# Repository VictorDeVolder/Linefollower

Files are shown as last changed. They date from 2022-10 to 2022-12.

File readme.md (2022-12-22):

# LineFollower
<br />
<br />
[picture]

<br />
<br />
  
## specifications
<br />
microcontroller: ATmega328 5V 16 MHz 
<br />
motors: Micro motor N20-BT21 9V-30:1-1000rpm
<br />
h-bridge: HALJIA DRV8833 1,5A 2 kanalen H-Bridge
<br />
sensors: QTR-8A reflectiesensorarray
<br />
batteries: 2x Quickstuff 18650 batterijen 
<br />
wireless communication: AZDelivery HC-05 Bluetooth module 
<br />
distance sensor - motors: 12,5cm 
<br />
weight: 210g
<br />
speed: 0,774 m/s 
<br />

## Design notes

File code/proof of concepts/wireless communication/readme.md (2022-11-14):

# draadloze communicatie proof of concept
minimale hard- en software waarmee aangetoond wordt dat duplex kan gecommuniceerd worden tussen de microcontroller en een smartphone, gebruik makend van HC-05 programma. 
<br />
### configuratie
Draadloze communicatie voor led aan/ uit zetten.

### opmerkingen
Correcte bautrate instellen.

### gebruiksaanwijzing
Zie datasheet.

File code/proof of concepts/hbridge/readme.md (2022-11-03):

# H-Bridge proof of concept

minimale hard- & software die aantoont dat 2 motoren onafhankelijk van elkaar kunnen draaien, en (traploos) regelbaar zijn in snelheid en draairichting.

aansturen van de DRV8833 H-brug

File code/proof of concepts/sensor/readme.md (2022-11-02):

# Sensoren proof of concept

minimale hard- en software die aantoont dat minimaal 6 sensoren onafhankelijk van elkaar kunnen uitgelezen worden en dat daarbij een zo groot mogelijk bereik van de AD converter benut wordt (indien van toepassing)

Uitlezing van 8 analoge sensoren: QRT-8a sensor

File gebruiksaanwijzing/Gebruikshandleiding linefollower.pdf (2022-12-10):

# Gebruikshandleiding linefollower

## Syntheseproject

Academiejaar 2022-2023

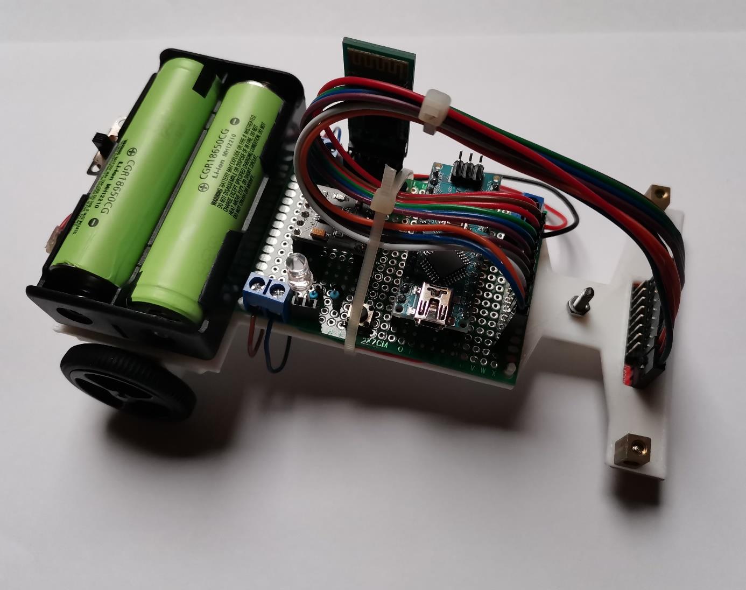
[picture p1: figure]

Naam: Victor De Volder

Klasgroep: 3AMB

Gebruikshandleiding linefollower:
Volg de volgende stappen om een correcte werking te bekomen.

Stap1:
Upload de finale code.

Stap2:
Schakel de hoofdschakelaar, deze bevindt zich achteraan de wagen.

Stap3: Connecteren
Download en open de app Serail Bluetooth Terminal. Klik op de navigation drawer en ga naar Devices. Connecteer vervolgens met de bluetooth module onder de naam HC-05 (98:D3:51:F5:EF:E6). Als alles goed verlopen is komt er in Terminal connected te staan.

Stap4: Commando’s

- Debug
Het commando debug geeft alle ingestelde parameters weer en de sensorwaarden.
- Set power, diff, kp, ki, kd, cycle.
De Set commando maakt het mogelijk om de ingestelde waardes van de weergegeven parameters te wijzigen.
- run
De linefollower begint te rijden.
- stop
De linefollower zal direct stoppen.
- Calibrate black
Zwart waarden kalibreren van de sensor.
- Calibrate white
Wit waarden kalibreren van de sensor.

Stap5: Kalibreren
Positioneer de sensoren boven een zwart vlak en voer het commando calibrate black uit in de Terminal. Breng vervolgens de sensoren boven een wit vlak en voer het commando calibrate white uit. De sensoren zijn nu gekalibreerd.

Stap6: Parameters instellen
Stel de gewenste parameters in met het commando Set … .

Ingestelde parameters:

- cycle time: 2000
- Power: 145
- diff: 0.20
- kp: 10
- ki: 0.20
- kd: 0.40

Stap7: Starten
Voer het commando run uit en de wagen zal de lijn beginnen volgen met een gemiddelde snelheid van 0.774 m/s.

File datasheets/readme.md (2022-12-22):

datasheets of the components used in this project

Datasheets zijn terug te vinden bij de proof of consepts.

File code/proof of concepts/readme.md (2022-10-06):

# Proof of Concepts

Een proof of concept is een combinatie van minimale hard- en software om eenvoudig aan te tonen dat iets werkt.  
Proof of concepts kunnen enerzijds als eerste poging dienen om een bepaald onderdeel van het project werkend te krijgen. Anderzijds kunnen ze tijdens het debuggen van het finale project dienen als test om eventuele hardware problemen te elimineren bij onduidelijke problemen.
<br />  
<br />
Een proof of concept bestaat uit
* een elektronisch schema (indien van toepassing)
* minimale code om de voorop gestelde zaken te demonstreren
* minimale uitleg / aandachtspunten
<br />
De elektronische schakelingen van de proof of concepts komen bij voorkeur overeen met deze van de uiteindelijke linefollower, zodat de code zonder aanpassingen op het finale project kan draaien.

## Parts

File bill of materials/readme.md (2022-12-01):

## bill of materials
<br />

|volgnummer|naam|omschrijving|nieuw/recup|kostprijs/stuk|aantal|subtotaal|
|---|----|---|---|---|---|---|
| 1| Micro motor N20-BT21 9V |  1000 rpm - 30:1  | nieuw | € 5,40 | 2  | € 10,80 |
| 2| 18650 batterijhouder dubbel |Lengte = 7,6cm; Breedte = 4,1cm; Hoogte = 2cm;| nieuw | € 1,39 | 1 | € 1,39 |
| 3| 2x Quickstuff 18650 batterijen plus oplader |2x 18650 3,7V 3000 mah oplaadbare batterijen | nieuw | € 22,95 | 1 | € 22,95 |
| 4| QTR-8A reflectiesensorarray - analoog - Pololu 960 | 8 sensoren; Analoog; Voedingsspanning: 5V of 3,3V | nieuw | € 11,91 | 1 | € 11,91 |
| 5| AZDelivery Nano V3.0 Mini USB Board | ATmega328 5V 16 MHz | nieuw | € 5,39 | 1 | € 5,39 |
| 6| HALJIA DRV8833 1,5A 2 kanalen H-Bridge | DC Gear motor driver module board; 2,7 tot 10,8V DC; Uitgangsstroom max 4A | nieuw | € 2,99 | 1 | € 2,99 |
| 7| Wielen 32x7mm Pololu | diameter 32mm, breedte 7mm | nieuw | € 4,32  | 2 | € 4,32 |
| 8| Akozon printplaat gatenroosterplaat | 5cm x 7cm dubbelzijdige prototyping-printplaat | nieuw | € 1,22 | 1 | € 1,22 |
| 9| Terminal blok connector | Pitch: 5,08mm; 5,08-301-2P, nominale spanning: 300V, nominale stroom: 16A | nieuw | € 0,27 | 3 | € 0,81 |
| 10| AZDelivery HC-05 Bluetooth Wireless RF Transceiver module | bereik max 10m, bluethooth klasse 2| nieuw | € 3,99 | 1 | € 3,99 |
| 11| Drukknopschakelaar | Bedrijfspanning = 250V; Connectortype = through hole; Merk Youmile  | recup | / | 1 | / |
| 12| Weerstand | 220 ohm | recup | / | 1 | / |
| 13| Weerstand | 1K ohm | recup | / | 4 | / |
| 14| Aan/ uit schakelaar batterij| / | recup | / | 1 | / |
| 15| Bout & moer | M5x22mm | recup | / | 1 | / |
| 16| Bout & moer | M2.5x14mm | recup | / | 6 | / |
| 17| Onderstel | PLA | recup | / | 1 | / |
| | | | | |Totaal | € 65,77 |

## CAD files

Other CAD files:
technische tekeningen/mechanisch/houder motor.ipt
technische tekeningen/mechanisch/onderplaat final.ipt

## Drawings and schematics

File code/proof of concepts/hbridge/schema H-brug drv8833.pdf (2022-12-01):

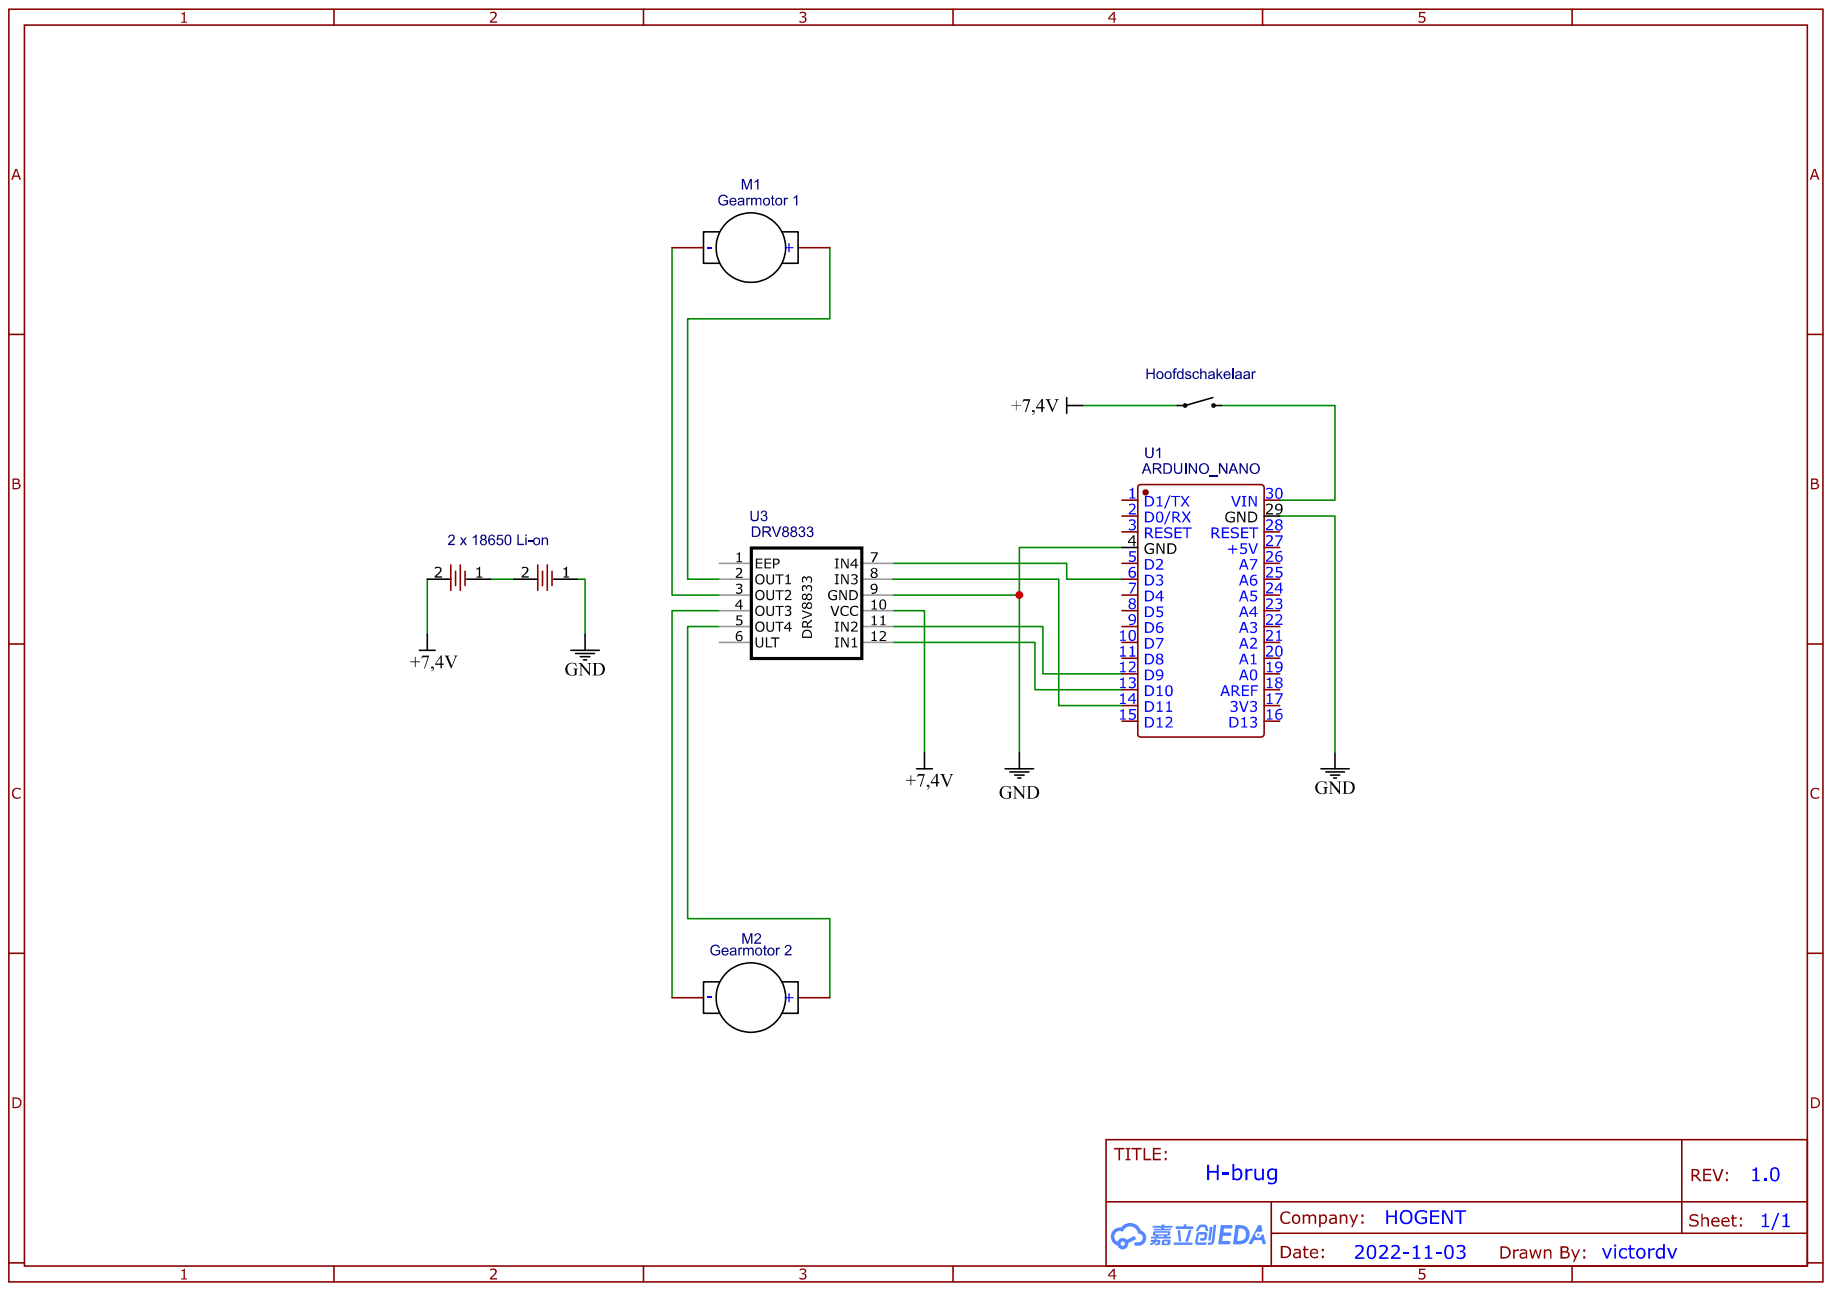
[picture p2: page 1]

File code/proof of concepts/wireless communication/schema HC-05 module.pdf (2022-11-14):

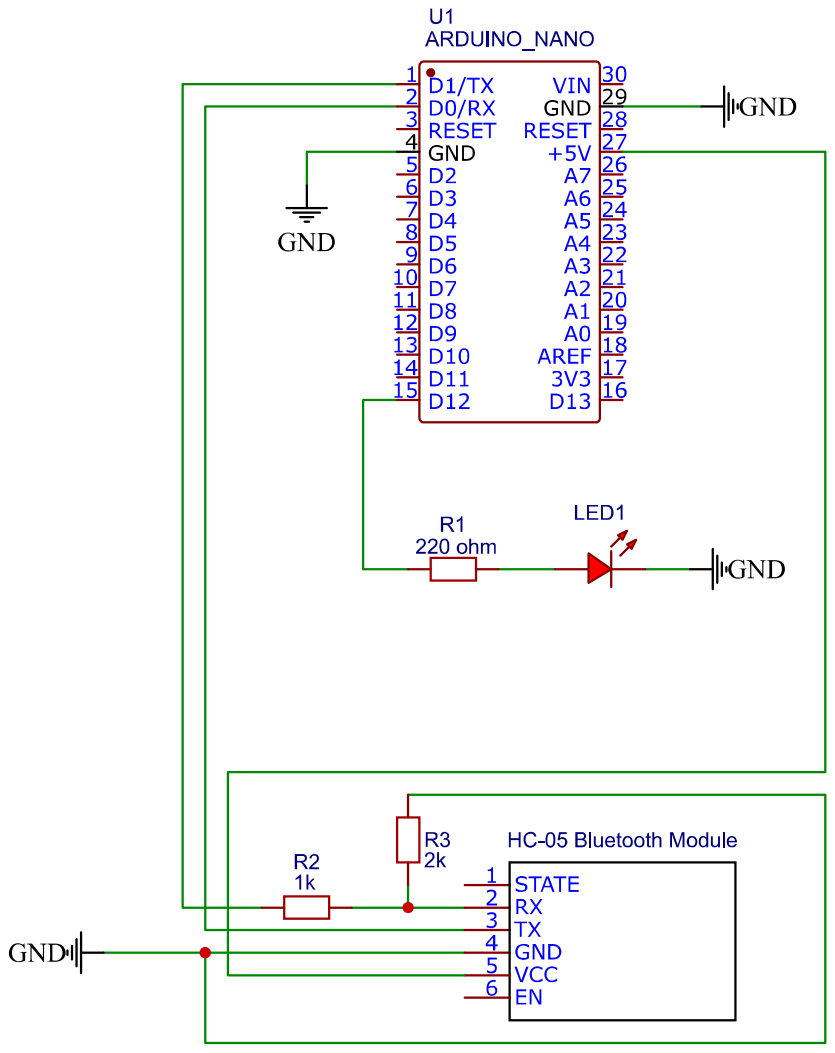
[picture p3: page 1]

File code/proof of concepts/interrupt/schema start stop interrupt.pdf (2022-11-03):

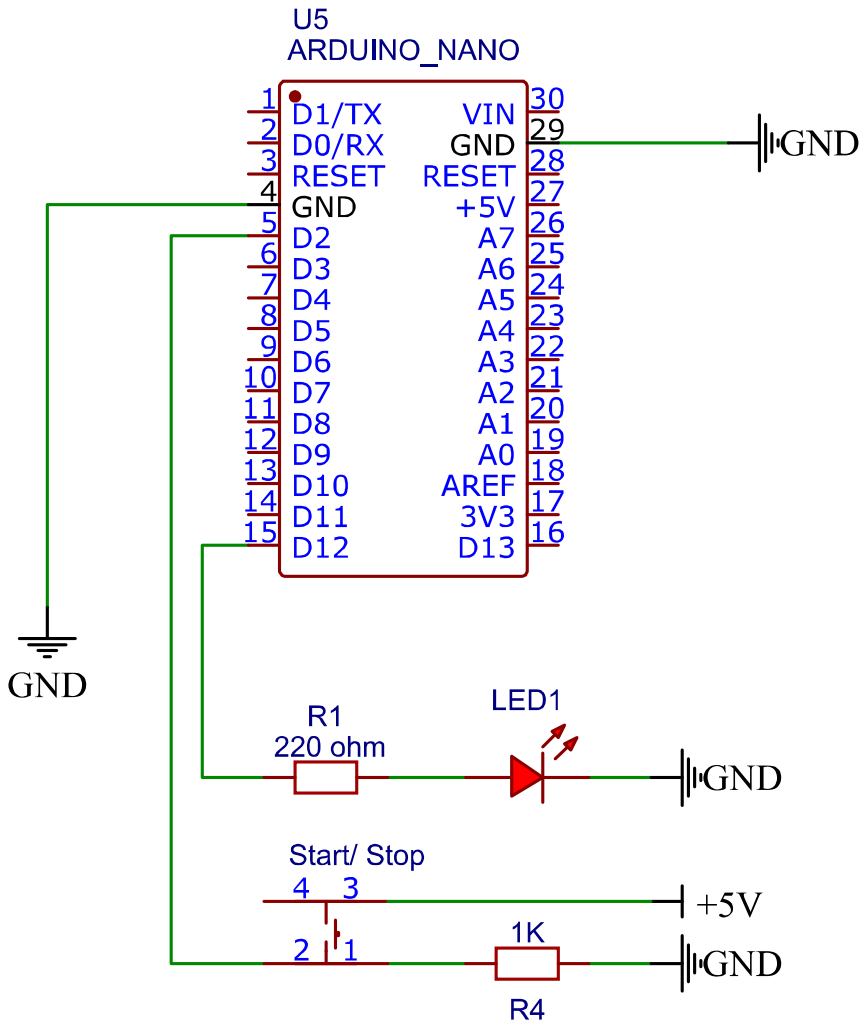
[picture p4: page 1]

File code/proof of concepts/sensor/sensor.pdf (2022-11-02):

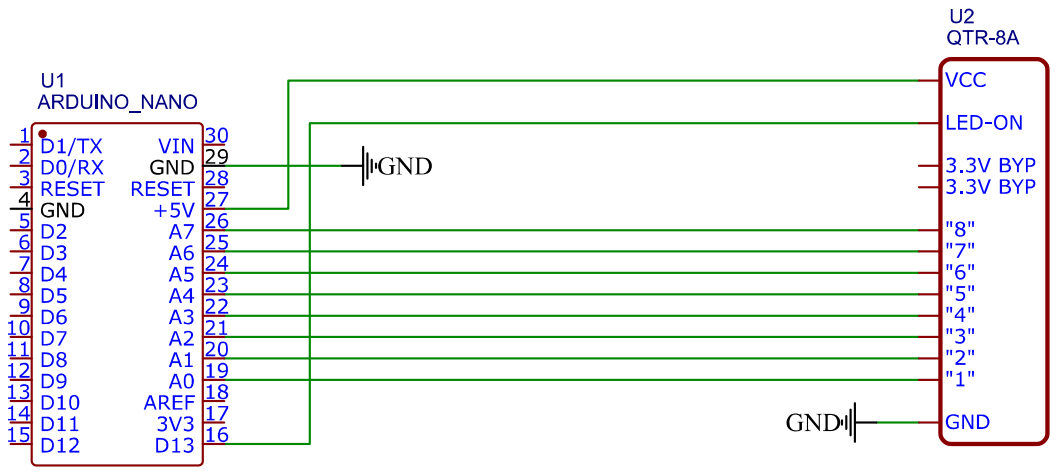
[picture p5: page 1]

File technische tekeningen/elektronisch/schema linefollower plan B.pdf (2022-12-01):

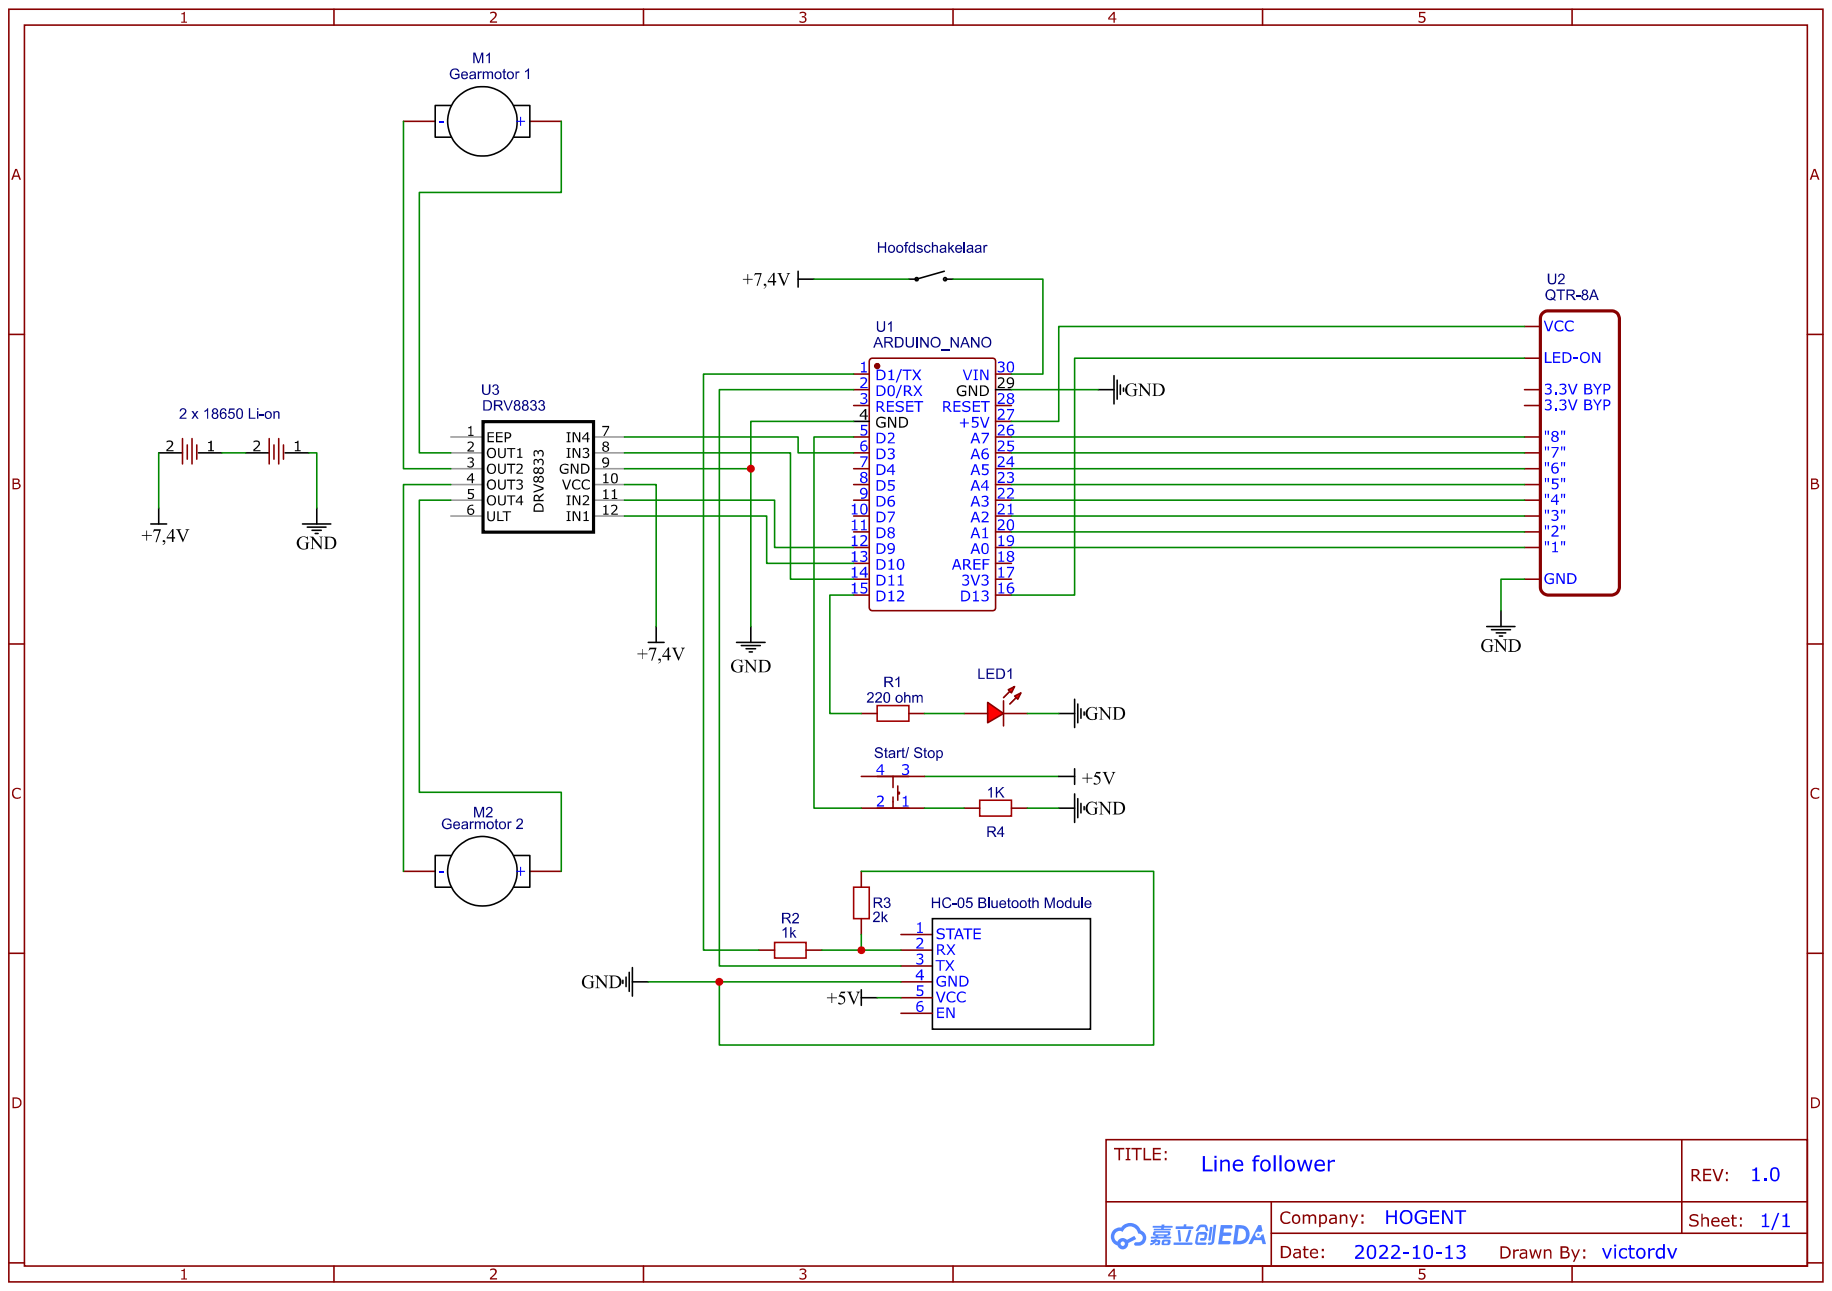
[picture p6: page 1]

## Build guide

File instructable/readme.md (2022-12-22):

# Instructable

Een instructable is een stappenplan - zonder verdere uitleg - hoe je vertrekkend van de bill of materials en gebruik makend van de technische tekeningen de robot kan nabouwen. Ook de nodige stappen om de microcontroller te compileren en te uploaden staan beschreven.

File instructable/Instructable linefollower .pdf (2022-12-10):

# Instructable linefollower

## Syntheseproject

Academiejaar 2022-2023


Naam: Victor De Volder

Klasgroep: 3AMB

## Inhoud

## 1: Inleiding

Voor het ontwerpen en bouwen van de Linefollower zijn er eerst enkele aspecten in acht genomen om een correcte werking te bekomen. Hierbij was het doel om een relatief modulaire linefollower te bouwen die binnen de gevraagde vereisten valt. Dit geeft de mogelijkheid om eenvoudig verandering door te voeren zoals bij defecte componenten of voor het optimaliseren van de linefollower.

## 2: Componenten

De benodigde componenten voor het bouwen van de linefollower zijn terug te vinden onder de map bill of materials.

## 3: Gereedschap

- Soldeerbout
- Kniptang
- Striptang
- Schroevendraaier
- Tang
- Multimeter

## 4: Ontwerp

### 4.1 Mechanisch

Op mechanisch vlak zijn er twee onderdelen ontworpen namelijk de onderplaat en de houders voor de motoren. Deze zijn geprint met een 3d printen en vervaardigd uit PLA met als voordelen licht van materiaal en heeft enige flexibiliteit. Verder is er rekening gehouden om het gewicht van de constructie zo laag mogelijk te houden en juist groot genoeg is om alle componenten er op te kunnen bevestigen.

De 3d tekeningen zijn terug te vinden in de GitHub onder de map technische tekeningen, mechanisch.

Onderplaat

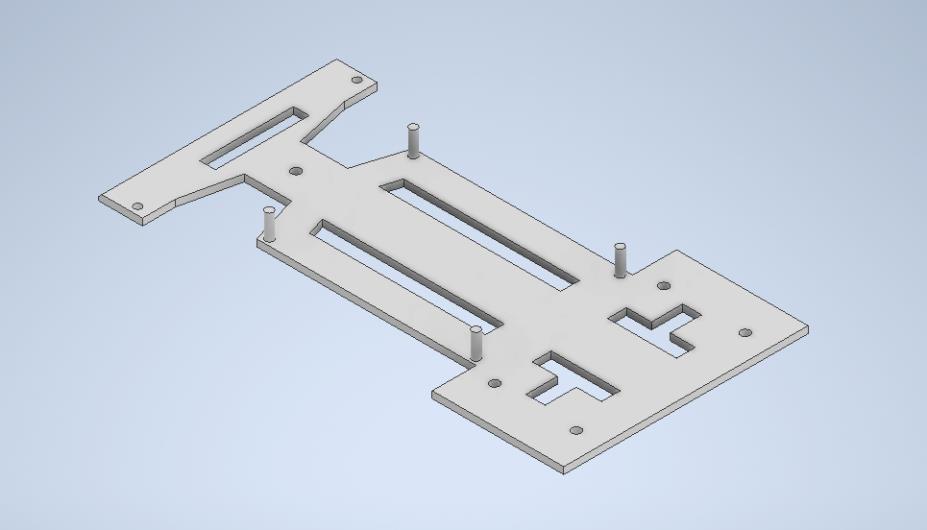
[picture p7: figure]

Houder motor

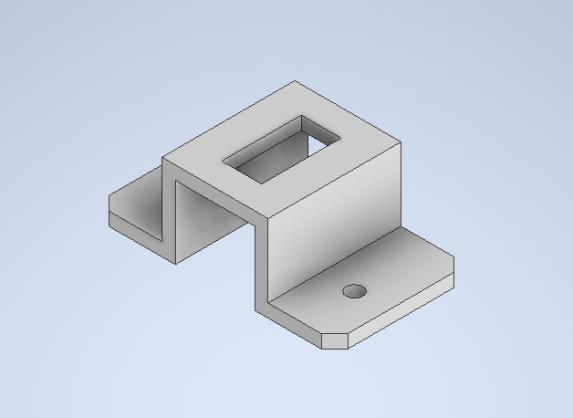
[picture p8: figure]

### 4.2 Elektrisch

Het elektronisch schema van plan B is terug te vinden in de GitHub onder de map technische tekeningen, elektronisch.

## 5: Montage linefollower

### 5.1: Stap1 printplaat

Positioneren van de female pinnen, terminal blok en drukknop:

De afmetingen van de printplaat zijn 5cm op 7cm. Hierbij is het belangrijk dat de female pinnen correct gepositioneerd worden zodat alle componenten op een logische manier er op bevestigd kunnen worden (zie elektronisch schema).

Opmerkingen:

- Hou er rekening mee dat de printplaat in het verlengde ligt van de onderplaat.
- Leg de female pinnen, de terminal blokken en de drukknop eerst uit voordat je begint te solderen.

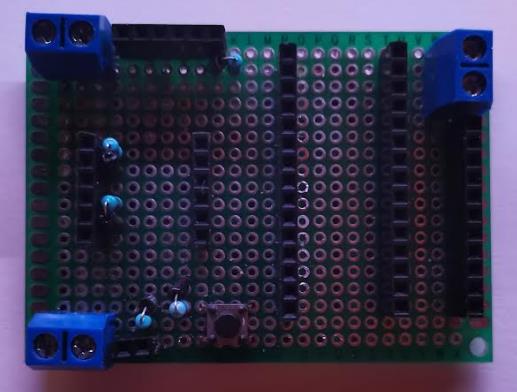
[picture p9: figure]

Verbindingen maken:

Na het solderen van de pinnen kan men nu beginnen met het solderen van de verbindingen. Knip de kabels op een juiste lengte en strip beide kanten. Probeer een bepaalde kleuren code te respecteren dit maakt alles duidelijker en eenvoudiger om fouten opsporen wanneer alles gesoldeerd is.

- Zwart = GND
- Rood = VCC/ 5V
- Groen = speeldraden

Opmerkingen:

- Zorg dat alle GND’s met elkaar zijn doorverbonden, ook de twee GND’s van de arduino Nano zelf.
- Meet alle verbindingen uit met de multimeter.

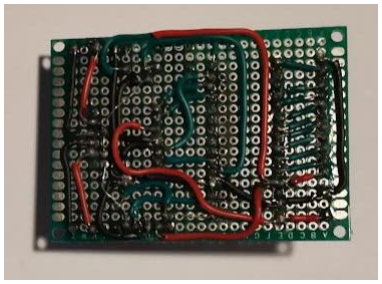
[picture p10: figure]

### 5.2: Stap2: componenten

Bevestiging van de componenten:

Plaats de H-brug, arduino Nano, bluetooth module en led op de female pinnen van de printplaat. Plaats dit vervolgens over de torens van de onderplaat zodat deze vast zit. Vervolgens kunnen de overige componenten op de onderplaat gemonteerd worden.

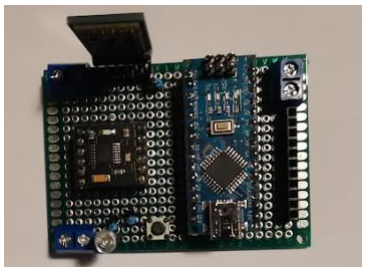
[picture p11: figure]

De baterijen worden in een batterijhouder geplaats en zijn bevestigt met klittenband op de onderplaat. Verder worden de motoren in de houders geplaats en worden gemonteerd met bouten en moeren aan de onderplaat achteraan.

De sensoren worden zo vooraan geplaats dat de pinnen perfect passen in de voorziene gleuf. Dit wordt net als voorgaande stap bevestigd met twee bouten en moeren.

Als laatste wordt er een bout en een moer vast gedraaid “op een gewenste hoogte” in de centraal geplaatste boring vooraan van de onderplaat.

### 5.3: Stap3: Doorverbinding

Overige componenten met elkaar doorverbinden:

Als laatste worden de motoren verbonden met de juiste terminal blok. De sensoren worden aangesloten met female, male connectoren en de batterij wordt eveneens aangesloten op de voorziene terminal blok die zich op de printplaat bevind.

Meet en controleer alles na, overloop het elektronisch schema nogmaals. Indien er geen problemen of bedenkingen worden waargenomen kan men overgaan tot de volgende stap.

### 5.4: Stap4: Programmatie

Proof of concepts & finale code:

De verschillende proof of concepts en de finale code zijn terug te vinden in de GitHub onder de map code.

Opmerkingen:

- Algemeen: Vooraleer men programma’s wilt uploaden in het programma Arduino. Zorg er voor dat de volgende zaken correct zijn ingesteld.
- Ga bij hulpmiddelen na of dat het board, processor en poort overeen komen. Indien dit niet het geval is pas dit aan.

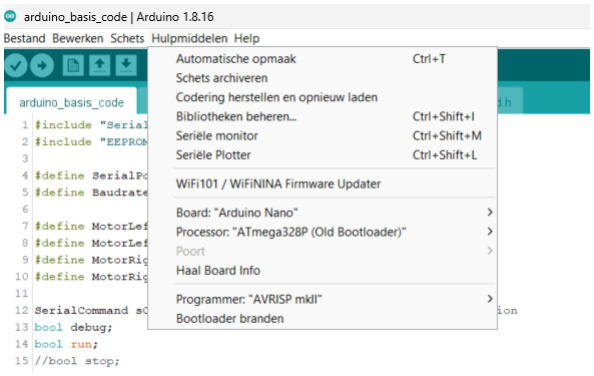
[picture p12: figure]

- Aangezien bij de HC-05 bluetooth module de TX en RX verbonden is met de RX en de TX pin van de Arduino Nano is het uploaden van een programma niet mogelijk. Wanneer de bluetooth module ontnomen wordt van de printplaat is het uploaden wel weer mogelijk. Na het uploaden van het programma kan de module terug geplaats worden zonder enige problemen.
- Zorg er voor dat de baudrate van het programma dezelfde is als van de bluetooth module, indien niet is draadloze communicatie niet mogelijk.

## 6: Testen

Ga nu de werking na van de H-brug, motoren, sensoren, bluetooth module, drukknop en led met de proof of consepts. Indien er geen problemen worden vastgesteld kan men overgaan tot het arduino basis programma en kan er geconcludeerd worden dat het praktische gedeelte werkt.

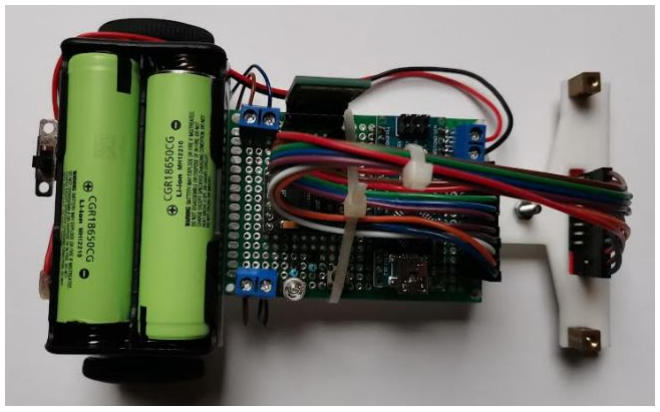
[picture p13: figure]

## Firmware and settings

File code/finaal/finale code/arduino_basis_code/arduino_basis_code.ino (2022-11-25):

#include "SerialCommand.h"
#include "EEPROMAnything.h"

#define SerialPort Serial
#define Baudrate 9600 

#define MotorLeftForward 3 
#define MotorLeftBackward 11
#define MotorRightForward 9   
#define MotorRightBackward 10

SerialCommand sCmd(SerialPort); // SerialCommand object declaration 
bool debug;
bool run;
//bool stop; 
unsigned long previous, calculationTime; 
float iTerm = 0;
float lastErr; 

//sensoren
const int sensor[] = {A7, A6, A5, A4, A3, A2, A1, A0};  
const int led = 12; 

const int Drukknop = 2; 


// EEPROM opgeslagen parameteres 
struct param_t
{
  unsigned long cycleTime; 
  /* andere parameters die in het eeprom geheugen moeten opgeslagen worden voeg je hier toe ... */
  int black[8];
  int white[8];
  int power; 
  float diff;
  float kp;  
  float ki; 
  float kd;
} params;

  int normalised[8];
  float debugPosition;
  float output;

//void onUnKnownCommand(char * command);
//void onSet();
//void onDebug();
//void onCalibrate();
//void onRun();

void setup()
{
  SerialPort.begin(Baudrate); // set serial baudrate at 115200

  sCmd.addCommand("set", onSet);
  sCmd.addCommand("debug", onDebug);
  sCmd.addCommand("calibrate", onCalibrate); 
  sCmd.addCommand("run", onRun);
  sCmd.addCommand("stop", onStop); 
  sCmd.setDefaultHandler(onUnknownCommand);
  EEPROM_readAnything(0, params);

  pinMode(13, OUTPUT);
  digitalWrite(13, HIGH);

  pinMode(12, OUTPUT); 
  pinMode(MotorLeftForward, OUTPUT);
  pinMode(MotorLeftBackward, OUTPUT);
  pinMode(MotorRightForward, OUTPUT);
  pinMode(MotorRightBackward, OUTPUT);
  
  SerialPort.println("ready");
}

void loop()
{
  sCmd.readSerial(); // listen and process serial commands
  
  unsigned long current = micros();
  if (current - previous >= params.cycleTime)
  {
    previous = current;

    //int normalised[8]; //?

    /* code die cyclisch moet uitgevoerd worden programmeer je hier ... */
    //SerialPort.print("normalised values: ");
    for (int i = 0; i < 8; i++)
    {
      normalised[i] = map(analogRead(sensor[i]), params.black[i], params.white[i], 0, 1000); 
    }

    float position = 0; // positie bepalen sensoren 
    int index = 0; // zwartste sensor bepalen 
    for(int i = 1; i < 8; i++) if (normalised[i] < normalised[index]) index = i; // nieuwe zwartste sensor zoeken 
    //SerialPort.println(normalised[index]);

    if (normalised[index] > 700) run = false; 

    if (index == 0) position = -30; 
    else if (index == 7) position = 30;
    else
    {
      int sensor_nul = normalised[index];
      int sensor_min_een = normalised[index-1];
      int sensor_plus_een = normalised[index+1];

      float b = sensor_plus_een - sensor_min_een;  // b berekenen 
      b = b / 2; 

      float a = sensor_plus_een - b - sensor_nul; 

      position = -b / (2 * a); 
      position += index;
      position -= 3.5;

      position *= 9.525;      
    }
    debugPosition = position; 
    
    /* normaliseren en interpoleren sensor */

    /* bereken error = setpoint - positie */
    float error = -position;

    /* proportioneel regelen */
    output = error * params.kp;

    /* integrerend regelen */
    iTerm += params.ki * error;
    iTerm = constrain(iTerm, -510, 510);
    output += iTerm;

    /* differentierend regelen */
    output += params.kd * (error - lastErr);
    lastErr = error; 
    
    /* aansturen motoren & begrenzen*/
    output = constrain(output, -510, 510); 
    
    int powerLeft = 0;
    int powerRight = 0;
    
    if (run) if (output >= 0)
    {
      powerLeft = constrain(params.power + params.diff * output, -255, 255); 
      powerRight = constrain(powerLeft - output, -255, 255); 
      powerLeft = powerRight + output; 
    }
    else
    {
      powerRight = constrain(params.power - params.diff * output, -255, 255); 
      powerLeft = constrain(powerRight + output, -255, 255); 
      powerRight = powerLeft - output;
    }

    //SerialPort.print("powerLeft");
    //SerialPort.println(powerLeft);
    
    //SerialPort.print("powerRight"); 
    //SerialPort.println(powerRight);
    
    //H-brug waardes wegschrijven 
    
    analogWrite(MotorLeftForward, powerLeft > 0 ? powerLeft : 0);
    analogWrite(MotorLeftBackward, powerLeft < 0 ? -powerLeft : 0);
    analogWrite(MotorRightForward, powerRight > 0 ? powerRight : 0);
    analogWrite(MotorRightBackward, powerRight < 0 ? -powerRight : 0);
  } 

  unsigned long difference = micros() - current;
  if (difference > calculationTime) calculationTime = difference;
}

void onUnknownCommand(char *command)
{
  SerialPort.print("unknown command: \"");
  SerialPort.print(command);
  SerialPort.println("\""); 
}
void onRun()
{
  run =true;
  digitalWrite(led, HIGH); 
}

void onStop()
{
  run =false; 
  digitalWrite(led, LOW);
}

void onSet()
{
  char* param = sCmd.next();
  char* value = sCmd.next();

  // ki

  if (strcmp(param, "cycle") == 0)
  {
    long newCycleTime = atol(value);
    float ratio = ((float) newCycleTime) / ((float) params.cycleTime);

    params.ki *= ratio;
    params.kd /= ratio; 

    params.cycleTime = newCycleTime;
  }
  else if (strcmp(param, "ki") == 0)
  {
    float cycleTimeInSec = ((float) params.cycleTime) / 1000000;
    params.ki = atof(value) * cycleTimeInSec;
  }
  else if (strcmp(param, "kd") == 0)
  {
    float cycleTimeInSec = ((float) params.cycleTime) / 1000000;
    params.kd = atof(value) / cycleTimeInSec;
  }

  else if (strcmp(param, "cycle") == 0) params.cycleTime = atol(value); // if 
  else if (strcmp(param, "power") == 0) params.power = atol(value); 
  else if (strcmp(param, "diff") == 0) params.diff = atof(value);
  else if (strcmp(param, "kp") == 0) params.kp = atof(value);
  /* parameters een nieuwe waarde geven via het set commando doe je hier ... */

  EEPROM_writeAnything(0, params);
}

void onDebug()
{
  SerialPort.print("cycle time: ");
  SerialPort.println(params.cycleTime);
  
  /* parameters weergeven met behulp van het debug commando doe je hier ... */
  SerialPort.print("black: ");
  for (int i = 0; i < 8; i++)
  {
    SerialPort.print(params.black[i]);
    SerialPort.print(" ");
  }
  SerialPort.println(" ");

  SerialPort.print("white: ");
  for (int i = 0; i < 8; i++)
  {
    SerialPort.print(params.white[i]);
    SerialPort.print(" ");
  }
  SerialPort.println(" ");

  SerialPort.print("normalised: ");
  for (int i = 0; i < 8; i++)
  {
    SerialPort.print(normalised[i]);
    SerialPort.print(" "); 
  }
  SerialPort.println(" ");

  SerialPort.print("output: ");
  SerialPort.println(output); 

  SerialPort.print("power: ");
  SerialPort.println(params.power);
  SerialPort.print("diff: ");
  SerialPort.println(params.diff);
  SerialPort.print("kp: ");
  SerialPort.println(params.kp);

  float cycleTimeInSec = ((float) params.cycleTime) / 1000000;
  float ki = params.ki / cycleTimeInSec;
  SerialPort.print("ki: ");
  SerialPort.println(ki);

  float kd = params.kd * cycleTimeInSec;
  SerialPort.print("kd: ");
  SerialPort.println(kd);
  
  SerialPort.print("calculation time: ");
  SerialPort.println(calculationTime);
  calculationTime = 0;
}
void onCalibrate()
{
  char* param = sCmd.next();

  if (strcmp(param, "black") == 0)
  {
    SerialPort.print("start calibrating black... ");
    for (int i = 0; i < 8; i++) params.black[i] = analogRead(sensor[i]);   
    SerialPort.println("done");
    
  }
  else if (strcmp(param, "white") == 0)
  {
    SerialPort.print("start calibrating white... ");
    for (int i = 0; i < 8; i++) params.white[i] = analogRead(sensor[i]);   
    SerialPort.println("done");
  }
  EEPROM_writeAnything(0, params);
}

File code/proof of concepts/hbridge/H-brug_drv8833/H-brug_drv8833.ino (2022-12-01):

int IN1 = 3; 
int IN2 = 11;
int IN3 = 9; 
int IN4 = 10;

const int drukknop = 2;
bool toestand_drukknop; 

void setup() {
  Serial.begin(9600); 

  pinMode(IN1, OUTPUT);
  pinMode(IN2, OUTPUT);
  pinMode(IN3, OUTPUT);
  pinMode(IN4, OUTPUT);
  pinMode(drukknop, INPUT);
  
}

void loop() {

  toestand_drukknop = digitalRead(drukknop); 

  if (toestand_drukknop == HIGH) 
  {

    //Voorwaarts 
    for(int i = 0; i <= 255; i++) 
    {
      analogWrite(IN1, i);
      analogWrite(IN2, 0);
      analogWrite(IN3, i);
      analogWrite(IN4, 0);
      delay(20);
    }
    
    for(int i = 255; i >= 0; i--) 
    { 
      analogWrite(IN1, i);
      analogWrite(IN2, 0);
      analogWrite(IN3, i);
      analogWrite(IN4, 0);
    }
    delay(3000); 

    //Achterwaarts  
    for(int i = 0; i <= 255; i++) 
    {
      analogWrite(IN1, 0);
      analogWrite(IN2, i);
      analogWrite(IN3, 0);
      analogWrite(IN4, i);
      delay(20);
    }
    
    for(int i = 255; i >= 0; i--) 
    { 
      analogWrite(IN1, 0);
      analogWrite(IN2, i);
      analogWrite(IN3, 0);
      analogWrite(IN4, i);
    }
    delay(3000); 

    //Motor rechts  
    for(int i = 0; i <= 255; i++) 
    {
      analogWrite(IN1, i);
      analogWrite(IN2, 0);
      analogWrite(IN3, 0);
      analogWrite(IN4, 0);
      delay(20);
    }
    
    for(int i = 255; i >= 0; i--) 
    { 
      analogWrite(IN1, i);
      analogWrite(IN2, 0);
      analogWrite(IN3, 0);
      analogWrite(IN4, 0);
    }
    delay(3000); 

        //Motor links  
    for(int i = 0; i <= 255; i++) 
    {
      analogWrite(IN1, 0);
      analogWrite(IN2, 0);
      analogWrite(IN3, i);
      analogWrite(IN4, 0);
      delay(20);
    }
    
    for(int i = 255; i >= 0; i--) 
    { 
      analogWrite(IN1, 0);
      analogWrite(IN2, 0);
      analogWrite(IN3, i);
      analogWrite(IN4, 0);
    }
    delay(3000); 
  }
}
